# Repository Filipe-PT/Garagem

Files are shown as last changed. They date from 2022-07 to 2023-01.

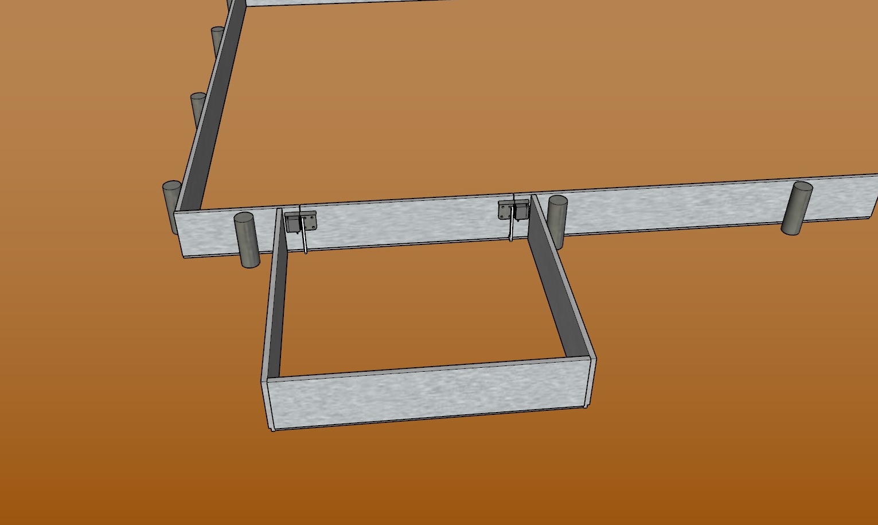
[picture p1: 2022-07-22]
Instalaçao rodapé - passo a passo/Instalação_rodapé_10_caixote_adicionado.jpg

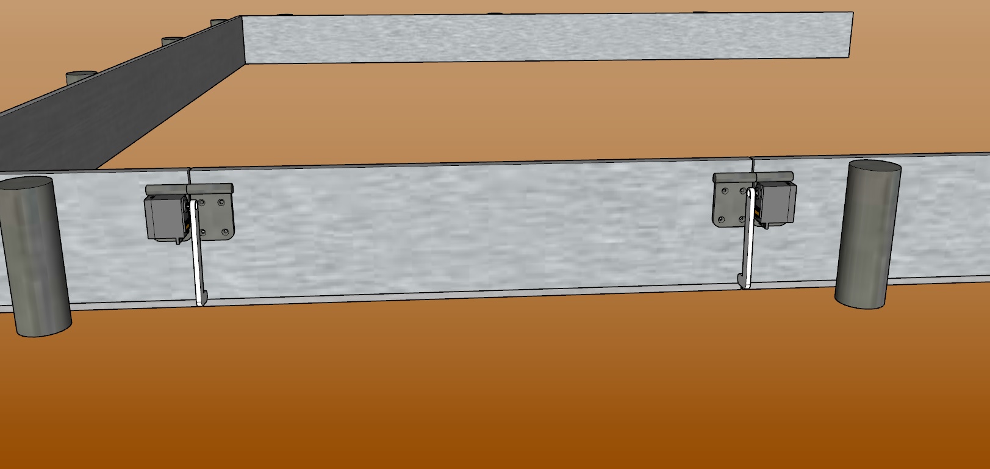
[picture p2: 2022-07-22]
Instalaçao rodapé - passo a passo/Instalação_rodapé_8.jpg

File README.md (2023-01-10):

# Garagem para o aspirador ! 

Olá, este projeto foi criado para aquelas pessoas que não tem grande local para guardar o seu robot aspirador e não gosta de o ver ali encostado a uma parede. A ideia foi então criar uma garagem para o guardar. Quando ele começa a trabalhar ( estado cleaning ) a porta da garagem abre acende a luz verde e ele sai, depois de um delay de 35 segundos ( pode ser alterado ) a porta fecha e a luz apaga, depois da aspiração terminar ( estado returning ), a porta volta a abrir mas neste caso acende a luz vermelha. Quando ele começa a carregar a porta fecha ( estado dock) e a luz apaga.
Deixo video de demonstração... nas pastas. 

# Requisitos:

- Home Assistent
- Addon ESPHome
- Integração NodeRed
- Robot integrado no Home Assistent

## Material :

- 2x [Servos](https://www.amazon.es/dp/B09WRBHSVD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)) ( usados neste projeto ).

- 1x [ESP32-WROOM-32](https://www.amazon.es/dp/B071P98VTG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) ( também funciona com [ESP8266](https://www.amazon.es/dp/B06Y1LZLLY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) ).

- 1x [Fita LED WS2812B ](https://pt.aliexpress.com/item/32682015405.html?pdp_npi=2%40dis%21EUR%21€%205%2C90%21€%203%2C89%21%21%21%21%21%40210318be16582511088073757e411e%2112000027369115512%21sh&spm=a2g0o.store_pc_home.productList_2400537.pic_0) ( foram usados somente 16 leds ).

- 2x [Reguladores de tensão  LM2596](https://amzn.to/2V7blBq) .

- 1x [Fonte Alimentação 12v](https://www.amazon.es/alimentación-universal-conmutación-cortocircuito-Sobrecarga/dp/B073GLDKMH/ref=sr_1_8?__mk_es_ES=ÅMÅŽÕÑ&crid=BHWZ3PO8ADGH&keywords=fuente%2Balimentación%2Bled%2B12v%2F24&qid=1658251483&s=lighting&sprefix=fuente%2Balimentacion%2Bled%2B12v%2F24%2Clighting%2C88&sr=1-8&th=1) ou [24v](https://www.amazon.es/Output-Supply-Converter-Adapter-Strips/dp/B01M4PI4E3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ón%2B24v&qid=1658251922&sr=8-10&th=1) .

- 2x [Dobradiças](https://www.leroymerlin.pt/Produtos/Ferragens/Ferragens-para-moveis/Dobradicas-de-movel/WPR_REF_15040256) . 

- 2x Braços para empurrar a porta da garagem.

## Esquema elétrico :

Existe várias maneira de o fazer neste repositório tem 2 soluções, uma mais económica, outra mais profissional, as duas funcionam bem por igual.
- [Solução económica ](https://im.ge/i/FOW8V4)
- [Solução profissional](https://im.ge/i/FOce7r)

## Instalação no móvel :

A instalação vai depender da imaginação de cada um, bem como o espaço que quer abrir, de salientar que neste projeto não foi estragado qualquer peça dos moveis da cozinha. Por isso, de hoje para amanhã é só desligar e tirar tudo e voltar a encaixar as peças do rodapé para ficar completamente de origem. Dentro do movel foi feita uma pequena "caixa" em U para ele não ir para debaixo do restante movel, podem ver na foto.

- [Local da instalação ](https://im.ge/i/FOgXwc)
- [Local interior ](https://im.ge/i/FOgo2T)

## Instalação Home Assistent :

Aqui no projeto vou deixar os códigos usados em ficheiro para adicionar na configuração do seu ESP32 no ESPHome. Também deixo aqui um flow para abrir/fechar e ligar/desligar a fita led com a cor verde/vermelho já preparado para adicionarem ao vosso NodeRed , bastando mudar as entidades para as vossas.

## Ter em ATENÇÃO :

Quando tiver tudo instalado, cabe a cada um ir aumentando o nível de abertura e fecho da porta no NodeRed, por segurança baixei os valores para não terem problemas, agora cabe a cada um ir aumentando e diminuindo esses valores consoante o vosso rodapé. Deixo foto a indicar onde têm de mudar esses valores ( ficheiro  alterarvalores.jpg e nivel.jpg ) dentro da pasta Flow NodeRed .

- [Alterarvalores.jpg](https://im.ge/i/FOgMAW)
- [Valores.jpg](https://im.ge/i/FOgQp0)

# Segurança:
Muito cuidado a mexer com corrente elétrica ... não me responsabilizo por qualquer dano causado.

# Agradecimentos :
Desde já agradeço a todos os membros que me ajudaram a realizar este projeto em ESPHome/NodeRed, já o tinha feito por outros caminhos que não este, tinha-o feito por um projeto já existente mas por mqtt.
Não vou citar nomes , quem ajudou sabe . Grande Abraço para todos e OBRIGADO

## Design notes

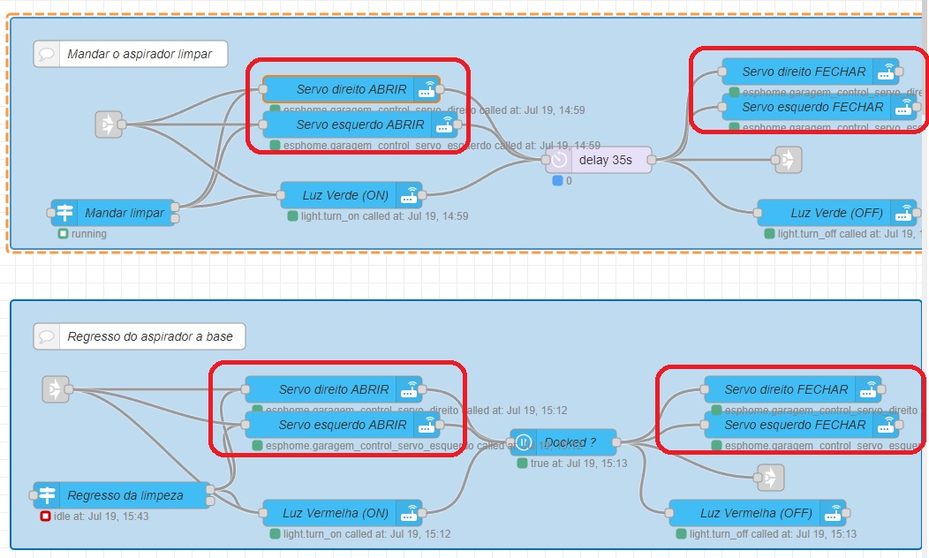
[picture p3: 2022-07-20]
Flow NodeRed/alterarvalores.jpg

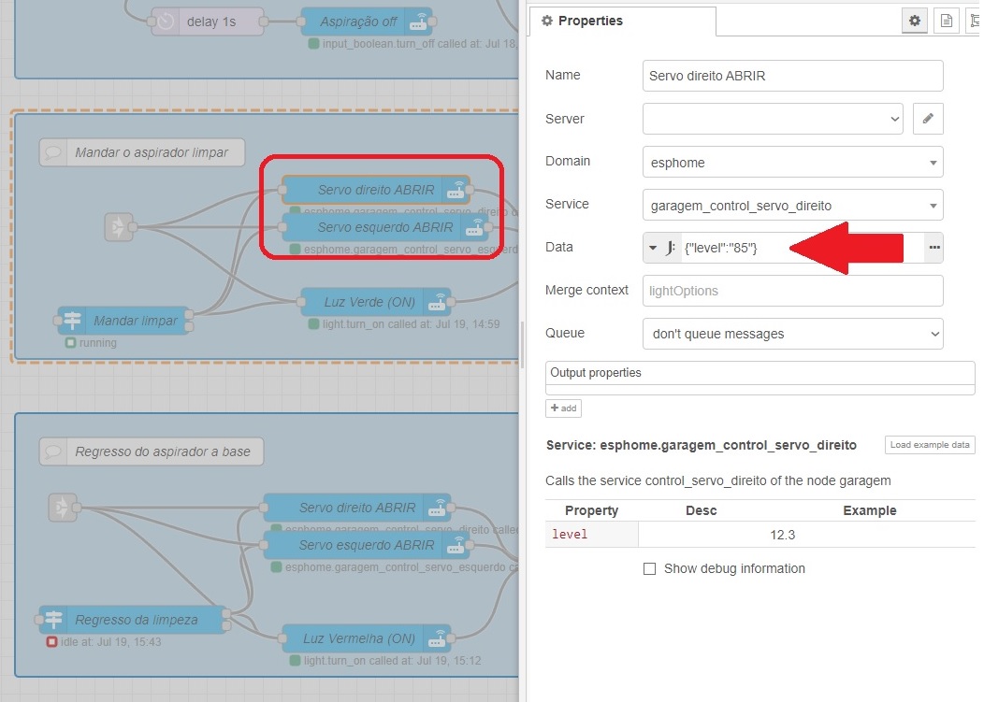
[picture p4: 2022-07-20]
Flow NodeRed/nivel.jpg

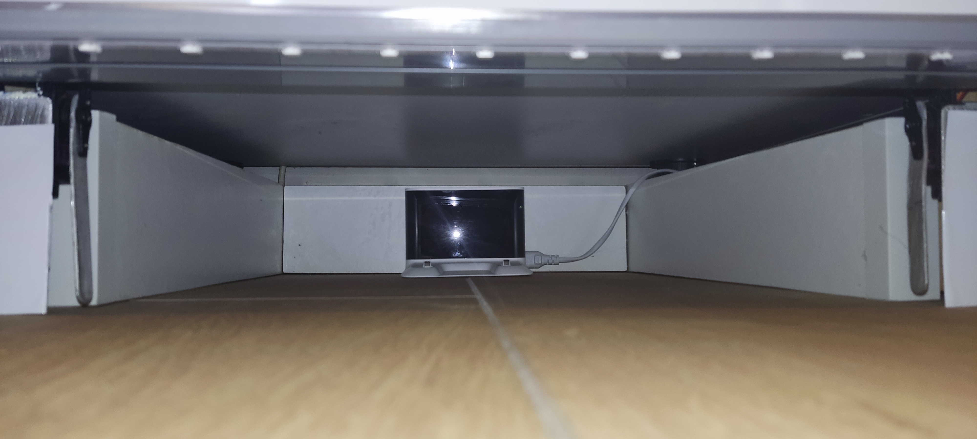
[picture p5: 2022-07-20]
Fotos/Interior garagem.jpg

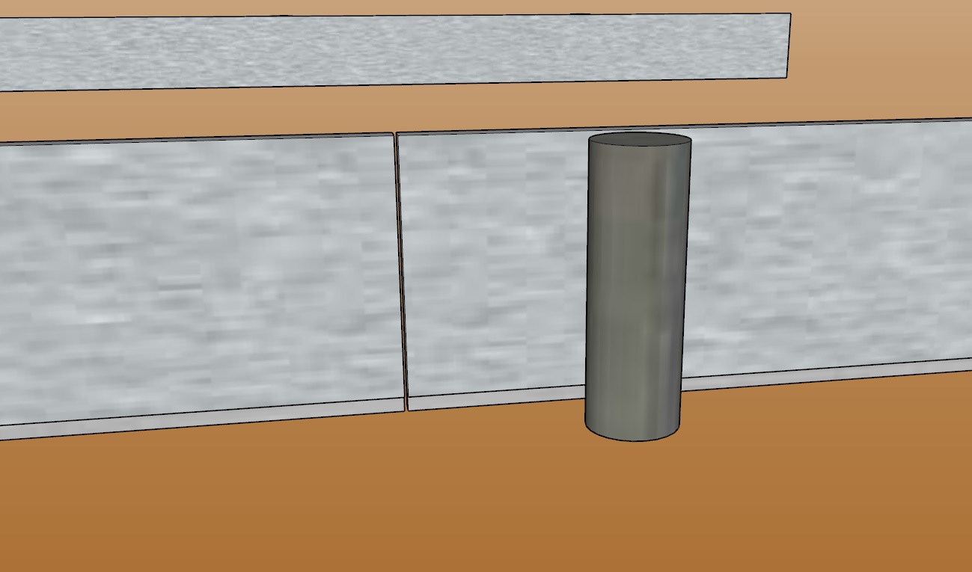
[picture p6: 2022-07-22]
Instalaçao rodapé - passo a passo/Instalação_rodapé_2.jpg

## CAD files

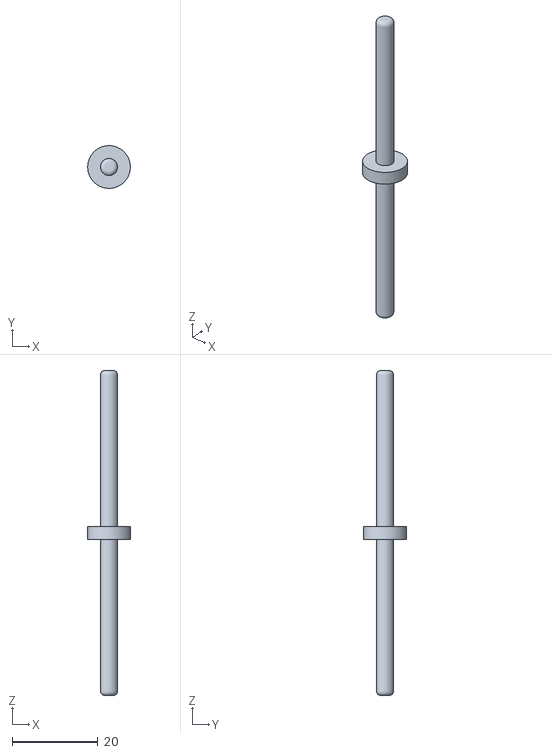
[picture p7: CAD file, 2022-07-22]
Peças para impressão 3D/Veio.stl
9.99 x 9.99 x 76.0

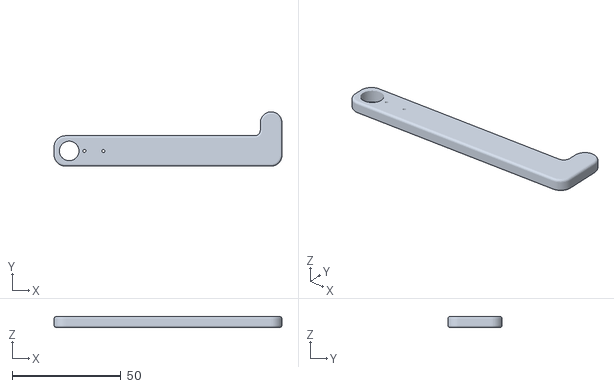
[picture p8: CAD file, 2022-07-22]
Peças para impressão 3D/Braço.stl
105.0 x 25.0 x 5.00

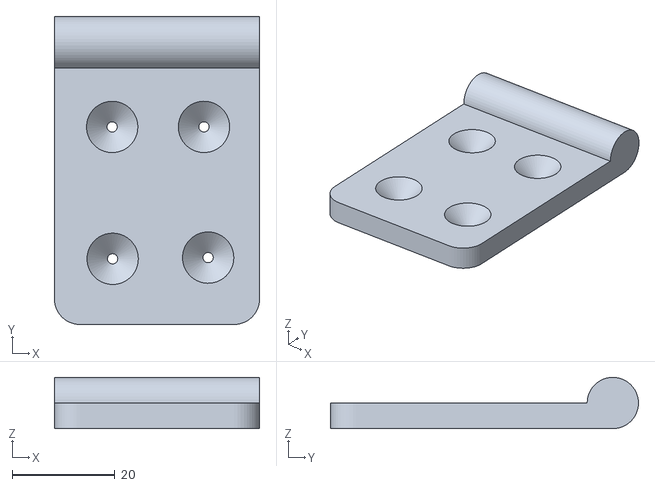
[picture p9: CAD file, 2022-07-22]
Peças para impressão 3D/Dobradiça_direita.stl
40.0 x 60.0 x 10.0

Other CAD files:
Peças para impressão 3D/Dobradiça_esquerda.stl

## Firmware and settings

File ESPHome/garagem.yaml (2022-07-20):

# Enable Home Assistant API
api:

  services:
    - service: control_servo_direito
      variables:
        level: float
      then:
        - servo.write:
            id: servo_direito
            level: !lambda 'return level / 100.0;'
  
    - service: control_servo_esquerdo
      variables:
        level: float
      then:
        - servo.write:
            id: servo_esquerdo
            level: !lambda 'return level / 100.0;'


#################################################################

captive_portal:

#### EFEITOS LUZ ####

light:
  - platform: fastled_clockless
    chipset: WS2812B
    pin: 5
    num_leds: 16
    rgb_order: GRB
    name: "Luz da Garagem"
    id: garage_led
    effects:
      - addressable_lambda:
          name: "Red" 
          update_interval: 150ms
          lambda: |-
            static int step = 0;
            static int direction = 1;

            if(initial_run){
                step = 0;
                it.all() = ESPColor(0,0,0);
            }

            it[step] = ESPColor(255,0,0);
            it[it.size() - step] = ESPColor(255,0,0);

            step = step + direction;

            if(step > it.size()/2){
                step = 0;
                it.all() = ESPColor(0,0,0);
            } 
      - addressable_lambda:
          name: "Green"
          update_interval: 150ms
          lambda: |-
            static int step = it.size()/2;
            static int step1 = it.size()/2;
            static int direction = 1;

            if(initial_run){
                step = it.size()/2;
                step1 = it.size()/2;
                it.all() = ESPColor(0,0,0);
            }

            it[step] = ESPColor(0,255,0);
            it[step1] = ESPColor(0,255,0);

            step = step + direction;
            step1 = step1 - direction;

            if(step > it.size()){
                step = it.size()/2;
                step1 = it.size()/2;
                it.all() = ESPColor(0,0,0);
            }

###### SERVOS ######

## Servo 1 ##
servo:
  - id: servo_direito
    output: servo_dir
    
###### Velocidade servo 1 ######    
    transition_length: 1s

## SERVO 2 ##
    
  - id: servo_esquerdo
    output: servo_esq
###### Velocidade SERVO 2 ######
    transition_length: 1s


###### OUTPUT ##########

output:
  - platform: ledc
    id: servo_dir
    pin: 4
    frequency: 50 Hz  
    
  - platform: ledc
    id: servo_esq
    pin: 18
    frequency: 50 Hz
    

            
